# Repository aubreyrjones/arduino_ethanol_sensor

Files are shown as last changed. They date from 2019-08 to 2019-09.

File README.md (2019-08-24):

Arduino Ethanol Controller
--------------------------

This is Arduino software for an automotive ethanol fuel sensor controller.

The ethanol sensor is designed to give real-time readings of ethanol content
in fuel as a percentage between 0 and 100%. It outputs this as an FM signal
from 50-150Hz, with the ethanol content given by subtracting 50 from the
signal frequency. The sensor itself runs on 12V, but outputs a 5V signal.
It also outputs fuel temperature readings, which are not used in this
project.

When adding an ethanol sensor to a vehicle that does not already support flex
fuel, there is unlikely to be an ECU input natively compatible with the
sensor's FM output. Instead, only a 0-5V analog input will be available. This
project converts the sensor signal to a voltage that the ECU can accept.

# Features

* Converts 50-150Hz square wave FM to a 0.5-4.5V signal
* Voltages below 0.5V and above 4.5V are used for error states (can be used to set DTC)
* "Sane" ethanol values within milliseconds of power-on from persistent memory
* All floating point math is `constexpr`, with no floating point operations occuring at runtime.

# Design

Depends on 16MHz/5V Arduino. CPU frequency is assumed fixed, with timing values computed
from CPU ticks.

This code assumes you are using an [I2C 12-bit DAC](https://www.sparkfun.com/products/12918) 
and a [I2C FRAM](https://www.adafruit.com/product/1895). Those links are to the breakout
boards used in prototyping this project's hardware. If you use those boards, be aware that
both of them have I2C pullup resistors. It is recommended that you desolder the pullup
resistors from the Adafruit board.

The FRAM chip/board may be omitted without altering the software. This will only affect 
the first fraction of a second after power up but before the sensor's 
readings have stabilized.

Electrical connection is simple. Wire the I2C lines, in parallel, to SDA/SCL of the Arduino.
The breakout boards can be stacked and soldered on a pair of header pins on the I2C, and short
wires for power. The breakout boards must be powered at 5V.

Wire the ethanol sensor to D8, with a 4.7kOhm pullup resistor in parallel. The ethanol sensor
should be powered at 12V.

Wire the DAC output to the ECU input.

The schematic below accurately describes the prototype circuit I have installed in my vehicle. 
The board design included in this repository is currently untested.

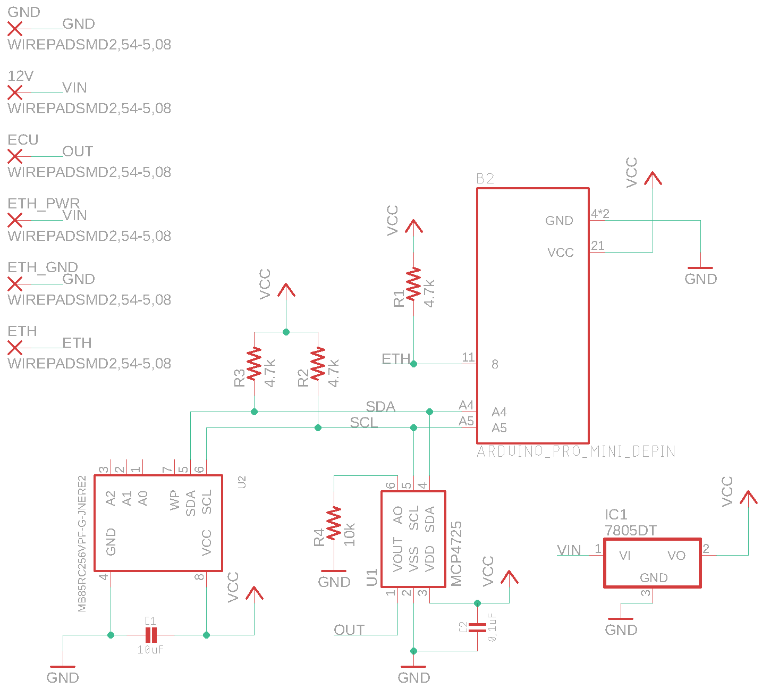
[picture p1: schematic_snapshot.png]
Circuit Schematic


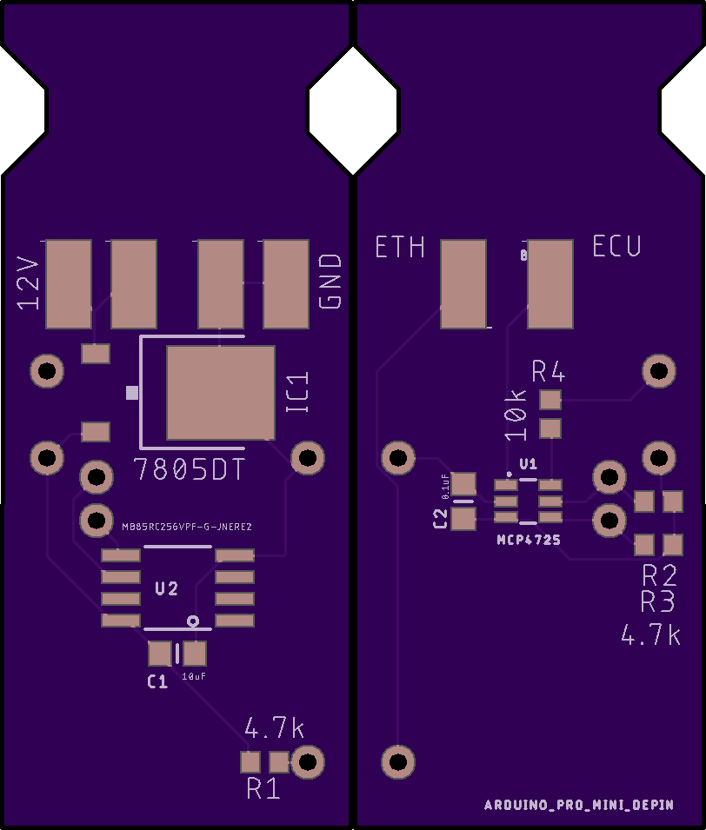
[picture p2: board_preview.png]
Board Preview


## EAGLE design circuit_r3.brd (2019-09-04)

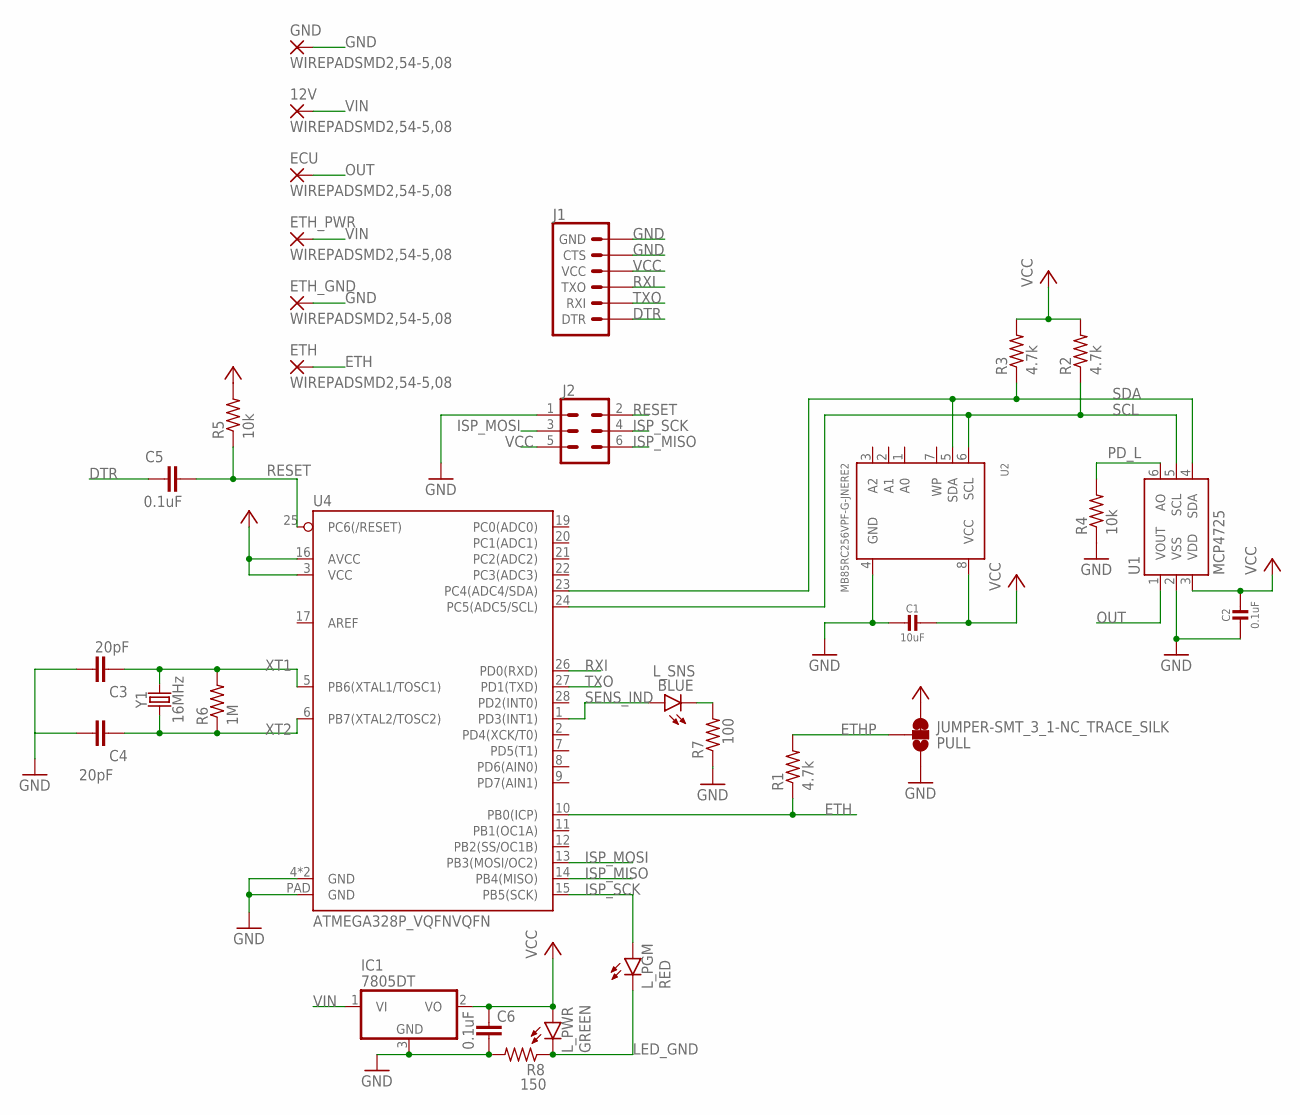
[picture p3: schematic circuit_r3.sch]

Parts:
12V: WIREPADSMD2,54-5,08; SMD2,54-5,08
C1: 10uF; _0805
C2: 0.1uF; _0603
C3, C4: 20pF; 0603
C5, C6: 0.1uF; 0603
ECU: WIREPADSMD2,54-5,08; SMD2,54-5,08
ETH: WIREPADSMD2,54-5,08; SMD2,54-5,08
ETH_GND: WIREPADSMD2,54-5,08; SMD2,54-5,08
ETH_PWR: WIREPADSMD2,54-5,08; SMD2,54-5,08
GND: WIREPADSMD2,54-5,08; SMD2,54-5,08
IC1: 7805DT; TO252
J1: 6_PIN_SERIAL_TARGETSILK; 6_PIN_SERIAL_TARGET_SIDE_W_SILK
J2: CONN_03X22X3_SILK_MALE_PTH; 2X3
L_PGM: RED; LED-0603
L_PWR: GREEN; LED-0603
L_SNS: BLUE; LED-0603
PULL: JUMPER-SMT_3_1-NC_TRACE_SILK; SMT-JUMPER_3_1-NC_TRACE_SILK
R1, R2, R3: 4.7k; R0603
R4, R5: 10k; R0603
R6: 1M; R0603
R7: 100; R0603
R8: 150; R0603
U1: MCP4725; SOT23-6
U2: MB85RC256VPF-G-JNERE2; SOIC8_208MIL
U4: ATMEGA328P_VQFNVQFN; VQFN-28
Y1: 16MHz; CRYSTAL-SMD-5X3.2-4PAD

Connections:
DTR: C5.2, J1.P$1 (DTR)
ETH: ETH.1, R1.1, U4.10 (PB0(ICP))
ETHP: PULL.2, R1.2
GND: C1.2, C2.2, C3.1, C4.1, C6.1, ETH_GND.1, GND.1, IC1.3 (GND), J1.P$5 (CTS), J1.P$6 (GND), J2.1, PULL.1, R4.1, R7.1, R8.2, U1.2 (VSS), U2.4 (GND), U4.4 (GND), U4.18 (GND), U4.PAD (GND)
ISP_MISO: J2.6, U4.14 (PB4(MISO))
ISP_MOSI: J2.3, U4.13 (PB3(MOSI/OC2))
ISP_SCK: J2.4, L_PGM.A, U4.15 (PB5(SCK))
LED_GND: L_PGM.C, L_PWR.C, R8.1
unnamed: L_SNS.C, R7.2
OUT: ECU.1, U1.1 (VOUT)
PD_L: R4.2, U1.6 (AO)
RESET: C5.1, J2.2, R5.1, U4.25 (PC6(/RESET))
RXI: J1.P$2 (TXO), U4.26 (PD0(RXD))
SCL: R2.1, U1.5 (SCL), U2.6 (SCL), U4.24 (PC5(ADC5/SCL))
SDA: R3.1, U1.4 (SDA), U2.5 (SDA), U4.23 (PC4(ADC4/SDA))
SENS_IND: L_SNS.A, U4.1 (PD3(INT1))
TXO: J1.P$3 (RXI), U4.27 (PD1(TXD))
VCC: C1.1, C2.1, C6.2, IC1.2 (VO), J1.P$4 (VCC), J2.5, L_PWR.A, PULL.3, R2.2, R3.2, R5.2, U1.3 (VDD), U2.8 (VCC), U4.3 (VCC), U4.16 (AVCC)
VIN: 12V.1, ETH_PWR.1, IC1.1 (VI)
XT1: C3.2, R6.2, U4.5 (PB6(XTAL1/TOSC1)), Y1.3 (2)
XT2: C4.2, R6.1, U4.6 (PB7(XTAL2/TOSC2)), Y1.1

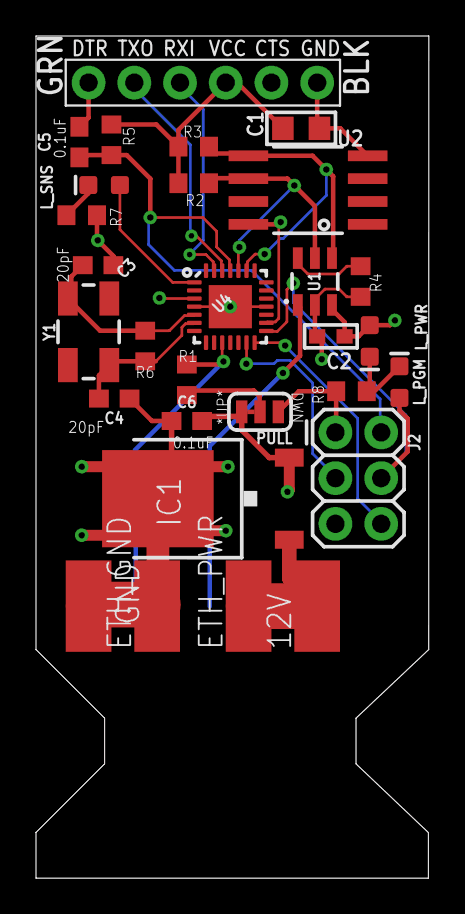
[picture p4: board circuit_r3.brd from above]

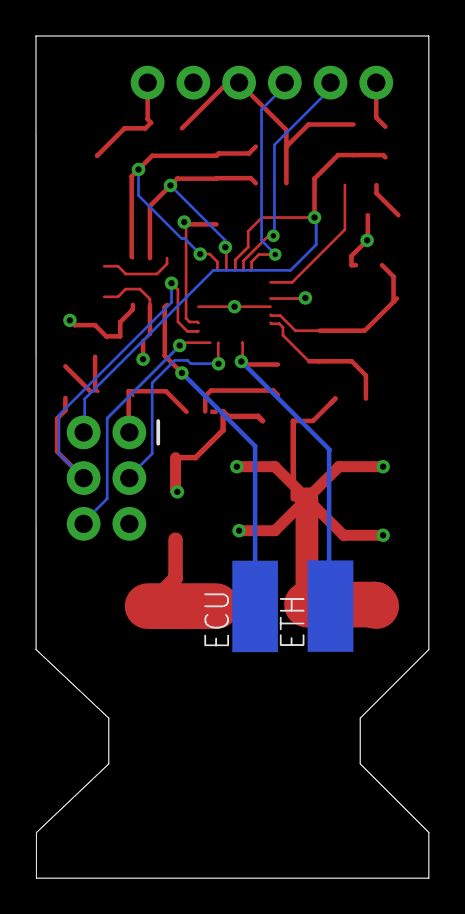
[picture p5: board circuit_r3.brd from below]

Board: 4 copper layers, 21.8 x 46.8 mm, 31 parts (2 on the bottom side), 21 nets.

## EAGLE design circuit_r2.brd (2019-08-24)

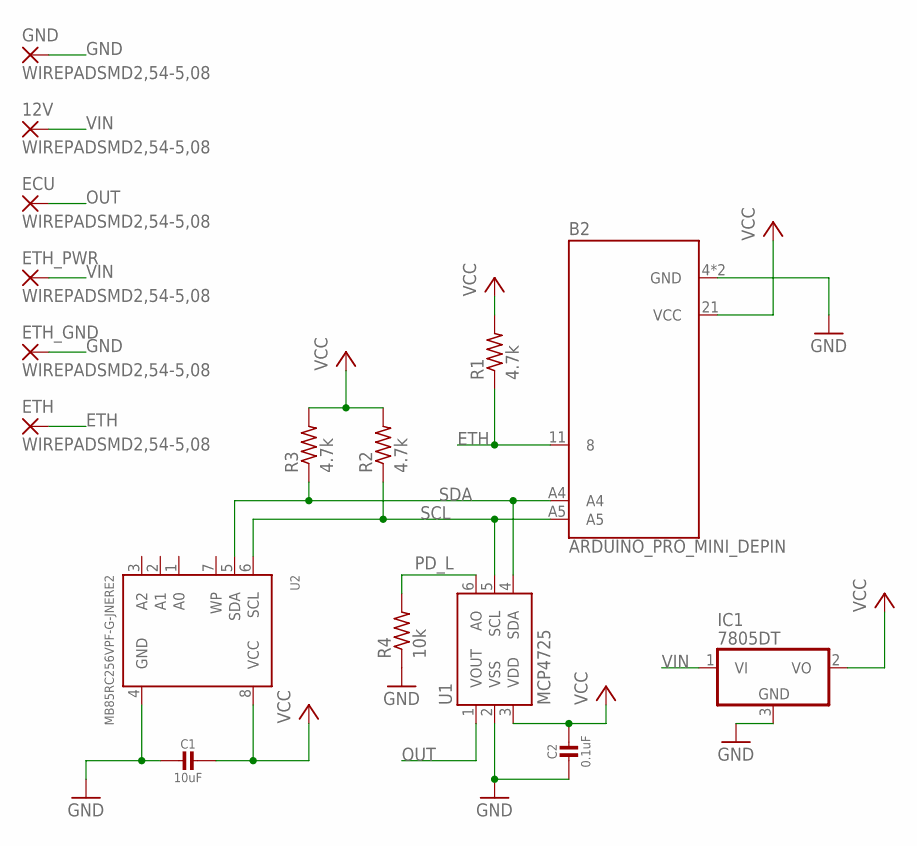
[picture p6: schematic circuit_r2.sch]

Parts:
12V: WIREPADSMD2,54-5,08; SMD2,54-5,08
B2: ARDUINO_PRO_MINI_DEPIN; ARDUINO_PRO_MINI
C1: 10uF; _0805MP
C2: 0.1uF; _0805MP
ECU: WIREPADSMD2,54-5,08; SMD2,54-5,08
ETH: WIREPADSMD2,54-5,08; SMD2,54-5,08
ETH_GND: WIREPADSMD2,54-5,08; SMD2,54-5,08
ETH_PWR: WIREPADSMD2,54-5,08; SMD2,54-5,08
GND: WIREPADSMD2,54-5,08; SMD2,54-5,08
IC1: 7805DT; TO252
R1, R2, R3: 4.7k; R0603
R4: 10k; R0603
U1: MCP4725; SOT23-6
U2: MB85RC256VPF-G-JNERE2; SOIC8_208MIL

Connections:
ETH: B2.11 (8), ETH.1, R1.1
GND: B2.4 (GND), B2.23 (GND), C1.2, C2.2, ETH_GND.1, GND.1, IC1.3 (GND), R4.1, U1.2 (VSS), U2.4 (GND)
OUT: ECU.1, U1.1 (VOUT)
PD_L: R4.2, U1.6 (AO)
SCL: B2.A5, R2.1, U1.5 (SCL), U2.6 (SCL)
SDA: B2.A4, R3.1, U1.4 (SDA), U2.5 (SDA)
VCC: B2.21 (VCC), C1.1, C2.1, IC1.2 (VO), R1.2, R2.2, R3.2, U1.3 (VDD), U2.8 (VCC)
VIN: 12V.1, ETH_PWR.1, IC1.1 (VI)

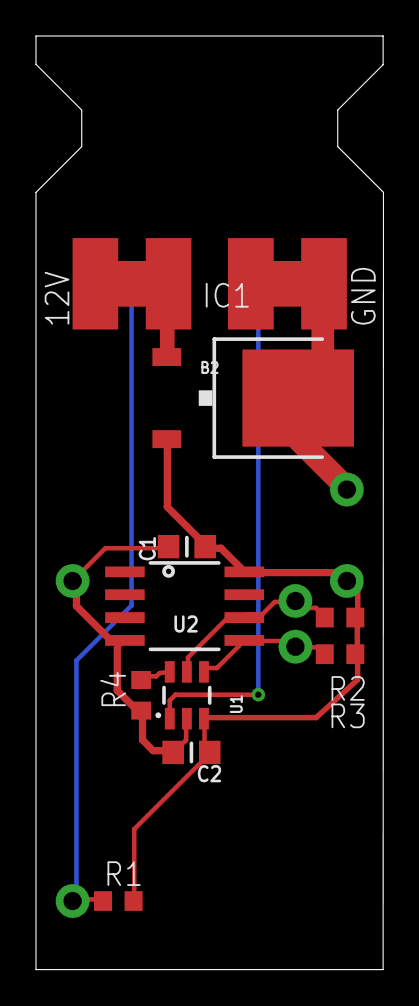
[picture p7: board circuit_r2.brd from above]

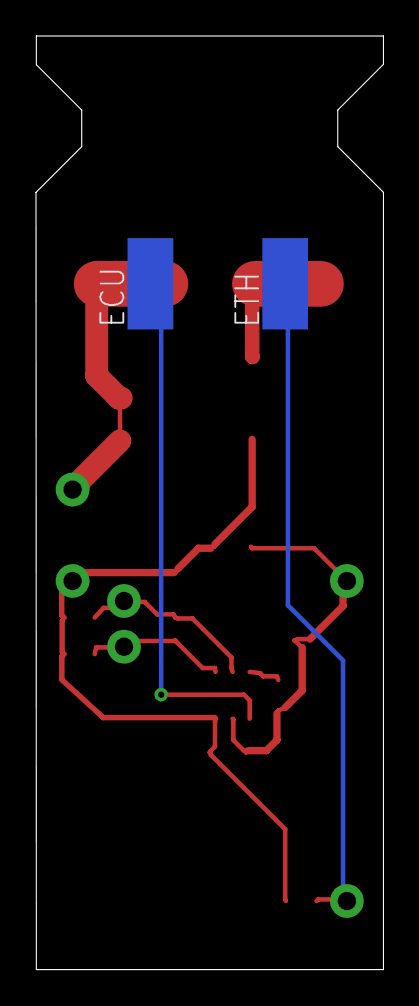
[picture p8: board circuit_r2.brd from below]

Board: 2 copper layers, 19.3 x 51.9 mm, 16 parts (2 on the bottom side), 8 nets.

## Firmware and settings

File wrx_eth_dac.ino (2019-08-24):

#include <Arduino.h>
#include <Wire.h>
#include <avr/builtins.h>
#include <avr/cpufunc.h>

#include <Adafruit_FRAM_I2C.h>

#define ETH_SERIAL_DEBUG

constexpr byte IN_PIN = 8;

// DAC chip
constexpr byte MCP4725_ADDR = 0x60;
constexpr byte DAC_WRITE_IMMEDIATE_COMMAND = 0x40;
constexpr byte DAC_CODE_WIDTH = 12;  // 12-bit DAC
constexpr uint16_t maxDAC = (1 << DAC_CODE_WIDTH);

// voltage limits and ranges
constexpr float MIN_ETH_VOLTAGE = 0.5f;
constexpr float MAX_ETH_VOLTAGE = 4.5f;
constexpr float MAX_VOLTAGE = 5.0f;

constexpr uint16_t vStep = round(maxDAC / MAX_VOLTAGE);

constexpr inline float clamp(float const& low, float const& high, float const& x) {
  return (low > x) ? low :
          (high < x) ? high : x;
}

constexpr inline uint16_t voltageToDAC(float const& v) {
  return round(clamp(0, MAX_VOLTAGE, v) * vStep);
}

constexpr uint16_t minEthDAC = voltageToDAC(MIN_ETH_VOLTAGE);
constexpr uint16_t ethVRange = voltageToDAC(MAX_ETH_VOLTAGE) - voltageToDAC(MIN_ETH_VOLTAGE);
constexpr uint16_t ethVStep = round(ethVRange / 100.0f);
constexpr uint16_t sensorErrorVoltage = voltageToDAC(5.0f);
constexpr uint16_t sensorNeverConnectedVoltage = voltageToDAC(0.10f);

// ethanol and controller state
int8_t ethanolPercentage = 0;

volatile bool framConnected = false;
volatile byte sensorErrorCount = 0;
volatile uint16_t sensorFrequency = 0;

// ethanol sensor frequency capture
void setupTimer()   // setup timer1
{
  TCCR1A = 0;      // normal mode
  TCCR1B = 0b11000100;    // rising edge trigger, Timer = CPU Clock/256, noise cancellation on
  TCCR1C = 0;      // normal mode
  TIMSK1 = 33;     // (00100001) Input capture and overflow interupts enabled
  TCNT1 = 0;       // start from 0
}

ISR(TIMER1_CAPT_vect)    // PULSE DETECTED!  (interrupt automatically triggered, not called by main program)
{
  uint16_t revTick = ICR1; // save duration of last revolution
  TCNT1 = 0;       // restart timer for next revolution
  
  if (revTick > 6500 || revTick < 250) { // 10-250 Hz "valid" range
    ++sensorErrorCount;
  }
  else {
    sensorErrorCount = 0;
    sensorFrequency = 62200 / revTick;
    return;
  }
}

ISR(TIMER1_OVF_vect)
{
  ++sensorErrorCount;
}

// === DAC ===
void dacOutImmediate(uint16_t const& dacCode) {
  Wire.beginTransmission(MCP4725_ADDR);
  Wire.write(DAC_WRITE_IMMEDIATE_COMMAND);
  Wire.write((byte) (dacCode >> 4));        // the 8 most significant bits...
  Wire.write((byte) ((dacCode & 15) << 4)); // the 4 least significant bits...
  Wire.endTransmission();

  #ifdef ETH_SERIAL_DEBUG
  Serial.print('d');
  Serial.println(dacCode);
  #endif
}

// === FRAM ====
Adafruit_FRAM_I2C fram = Adafruit_FRAM_I2C();

void persistToFRAM(int8_t value) {
  fram.write8(23, value);
}

int8_t fetchFromFRAM() {
  return fram.read8(23);
}

// == ethanol and filtering ==
constexpr uint16_t ethanolToDAC(int8_t const& eth) {
  return eth * ethVStep + minEthDAC;
}

bool updateEthanol() {
  uint16_t freqSample = sensorFrequency; // local copy of volatile

  if (freqSample >= 50 && freqSample <= 150) {
    ethanolPercentage = freqSample - 50;

    return true;
  }

  return false;
}

void outputEthanol() {
  dacOutImmediate(ethanolToDAC(ethanolPercentage));
}

void setup() {
  #ifdef ETH_SERIAL_DEBUG
  Serial.begin(115200);
  #endif

  pinMode(IN_PIN, INPUT);
  setupTimer();

  Wire.begin();
  Wire.setClock(400000);

  if (fram.begin()) {
    framConnected = true;

    int8_t savedEth = fetchFromFRAM();
    if (savedEth >= 0 && savedEth <= 100) {
      ethanolPercentage = savedEth;
      outputEthanol(); // drive the saved value immediately since it appears valid.
    }
  }
}

void loop() {
  static bool sensorErrorState = false;
  static unsigned long lastSampleTime = 0;

  if (!sensorErrorCount) { // we've got good sync, or we haven't overflowed yet
    sensorErrorState = false;

    if (updateEthanol()) { // the ethanol has been updated from the sensor
      lastSampleTime = millis(); // save the time (good for 50 days continuous)
      if (framConnected) {
        persistToFRAM(ethanolPercentage); // store this last reading to the FRAM 
      }
    }
  }
  else if ((!framConnected && !lastSampleTime) || // no sync, never sync'd, and no FRAM
            ((millis() - lastSampleTime) > 2000)) { // or we've spent 2 seconds with no sensor
    sensorErrorState = true; // immediate error
  }
  
  if (!sensorErrorState) {
    outputEthanol();
    
    #ifdef ETH_SERIAL_DEBUG
    Serial.println(ethanolPercentage);
    Serial.print('f'); Serial.println(sensorFrequency);
    #endif
  }
  else {
    uint16_t errorVoltage;
    
    #ifdef ETH_SERIAL_DEBUG
    char errorChar;
    #endif

    if (lastSampleTime) {
      errorVoltage = sensorErrorVoltage;
      
      #ifdef ETH_SERIAL_DEBUG
      errorChar = 's';
      #endif
    }
    else {
      if (framConnected) {
        errorVoltage = sensorNeverConnectedVoltage;
      }
      else {
        errorVoltage = 0;
      }
      
      #ifdef ETH_SERIAL_DEBUG
      errorChar = 'c';
      #endif
    }

    dacOutImmediate(errorVoltage);

    #ifdef ETH_SERIAL_DEBUG
    Serial.println('n');
    #endif
  }
  
  delay(100);
}

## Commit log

2019-08-10 Updated to fixed point, constexpr, and better error handling.
    [wrx_eth_dac.ino]
2019-08-10 Added beginning of readme, partial circuit.
    [circuit.sch]
2019-08-10 Working on the schematic.
    [circuit.sch]
2019-08-11 Added schematic and board design.
    [circuit.brd, circuit2.brd, circuit_1layer.brd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]
2019-08-11 Added board preview.
2019-08-11 Updated README to describe schematic and pcb state.
2019-08-11 Switched to rising edge pulse detection to avoid jitter from the PWM temp reading.
    [wrx_eth_dac.ino]
2019-08-24 Working on a version without the promini.
    [circuit_r2.brd, circuit_r2.sch, circuit_r3.brd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]
2019-08-24 Oooh, getting close.
    [circuit_r3.brd, circuit_r3.sch]
2019-08-24 trying to make it smaller.
    [circuit_r3.brd]
2019-08-24 pre autoroute
    [circuit_r3.brd]
2019-08-24 More revisions...
    [circuit_r3.brd, circuit_r3.sch]
2019-08-25 Pretty good design.
    [circuit_r3.brd, circuit_r3.sch]
2019-08-26 Production prototype, including indicator leds.
    [circuit_r3.brd, circuit_r3.sch]
2019-09-04 More fiddling with the r3 board.
    [circuit_r3.brd]

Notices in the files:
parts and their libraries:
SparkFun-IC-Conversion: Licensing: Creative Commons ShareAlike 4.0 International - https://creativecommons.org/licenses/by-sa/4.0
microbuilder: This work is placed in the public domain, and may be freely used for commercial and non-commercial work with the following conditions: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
